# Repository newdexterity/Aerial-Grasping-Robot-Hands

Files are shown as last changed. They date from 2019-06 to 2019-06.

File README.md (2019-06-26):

# Aerial-Grasping-Robot-Hands
## Introduction
Over the last decade, a new class of adaptive robot hands has been proposed that facilitates the execution of stable grasps in unstructured environments even when the object properties are not known. This attribute of adaptive hands is due to the under-actuation and their mechanical compliance that allow them to conform to the object surface. 

This adaptive robot hand is designed for UAV-based autonomous package delivery problem. Therefore, the robot hand must be extremely quick (< 100 ms), [lightweight](https://github.com/newdexterity/Aerial-Grasping-Robot-Hands/blob/master/Media/weight_analysis_aerial_gripper.pdf) (< 505 g), provide reliable grasping and enable perching for aerial platforms such as UAVs.

## Prototype
The prototype of this aerial grasping robot hand is designed by [New Dexterity Research Team](https://www.newdexterity.org/) from the University of Auckland.

<p align="center">
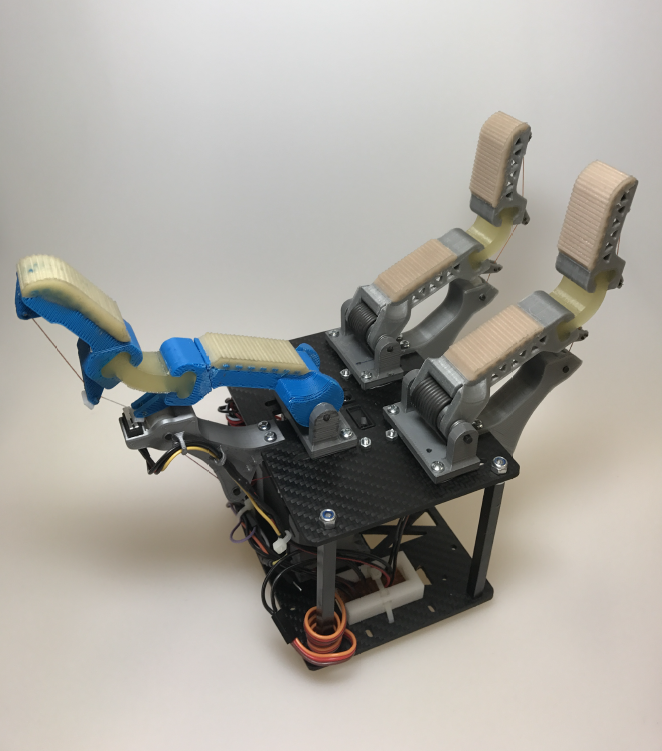
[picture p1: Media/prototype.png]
  
</p>

<p align="center"> 
  Figure 1. Prototype of the aerial grasping robot hand
</p>

## Quick release mechanism
A novel quick release mechanism which contains two servomotors has been proposed in this paper. The quick release mechanism allows the main servomotor to winch the tendons and open each finger. When the other servomotor is actuated, the dog collar disengages with the 35T spur gear, allowing the dog collar and the drum to rotate freely.

<p align="center">
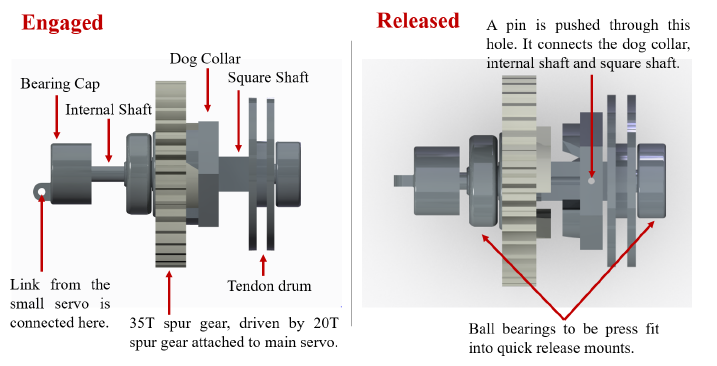
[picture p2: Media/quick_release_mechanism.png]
  
</p>

<p align="center"> 
  Figure 2. Quick release mechanism
</p>                                           

## Sensors
* [Infrared sensor](http://www.sharp-world.com/products/device/lineup/data/pdf/datasheet/gp2y0a21yk_e.pdf)

## Contents
In this repository you can find:
* CAD files of an ultra-fast aerial grasping robot hand
* Archive of prototype images
* Arduino code for controling this robot hand

## Notes
Please open a [Github issue](https://github.com/newdexterity/Aerial-Grasping-Robot-Hands/issues) if you encounter any problem.

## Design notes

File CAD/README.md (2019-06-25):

## Robot Hands CAD files
In this folder we provide appropriate 3D models (Solidworks .SLDPRT) and files for 3d printer (.stl) in order to replicate the proposed design. This aerial grasping robot hand has an improved mechanical structure design and a shell to protect the quick release mechanism compared with the prototype.

<p align="center">
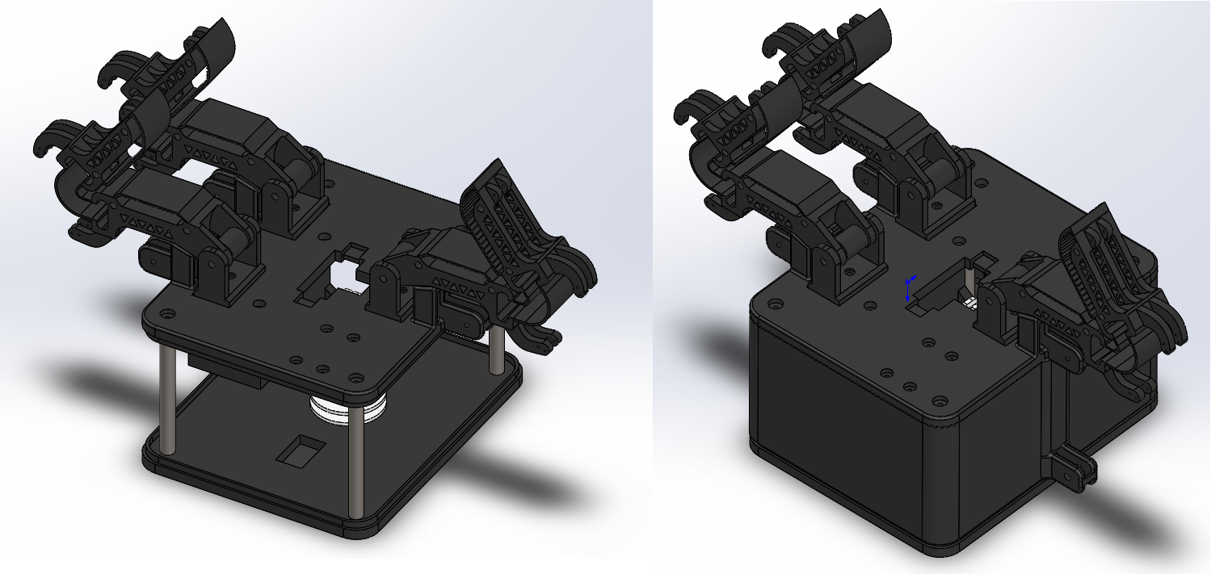
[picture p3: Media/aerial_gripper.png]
  
</p>

<p align="center"> 
  Figure 3. The appearance of the aerial grasping robot hand.
</p>    
                                           
## Modeling
If you need some help on modeling fingers, please take a look at the instruction [here](https://www.eng.yale.edu/grablab/openhand/OpenHand%20Finger%20Guide.pdf).

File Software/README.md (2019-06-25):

## Introduction
In order to control the robot hand, we use one OpenCM9.04-C board and two Dynamixel motors (XM430-350-T). Please click [here](http://www.robotis.us/dynamixel/) for more information about Dynamixel motors.
## OpenCM9.04
OpenCM9.04 is a microcontroller board based on 32bit ARM Cortex-M3. The OpenCM9.04’s schematics and source codes are open-source. Please click [here](http://emanual.robotis.com/docs/en/parts/controller/opencm904/) for more information about OpenCM9.04.

The connections between OpenCM9.04-C board and other devices are shown in Fig. 4:
<p align="center">
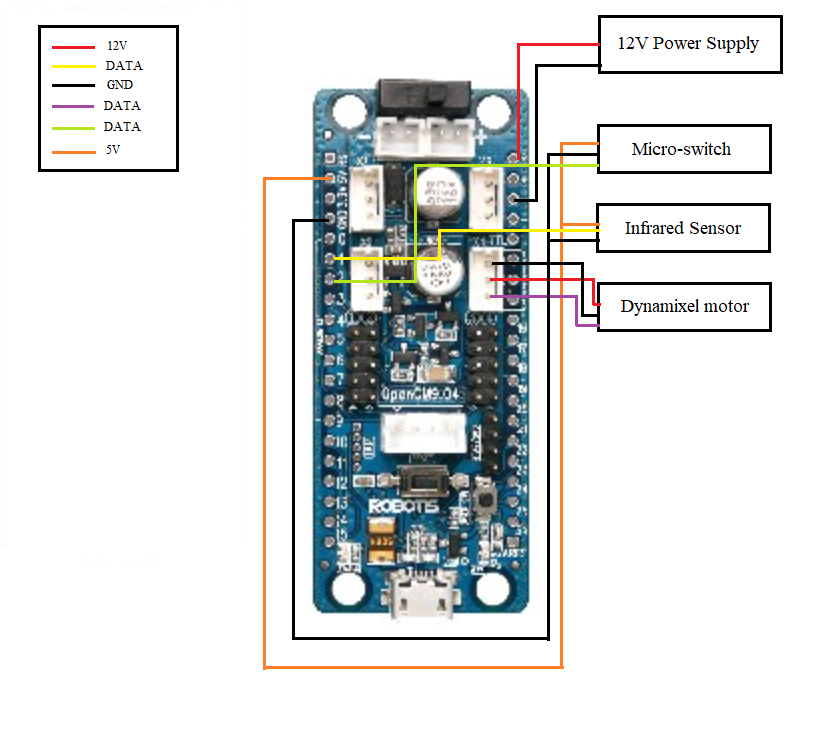
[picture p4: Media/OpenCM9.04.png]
  
</p>

<p align="center"> 
  Figure 4. Connections between OpenCM9.04-C and other devices.
</p>   
                                        
## IDE
As OpenCM IDE will not be updated anymore, we recommend users to code on Arduino IDE for OpenCM9.04-C board. Here is the instruction for installing OpenCM9.04 package on Arduino IDE:

<p align="center">
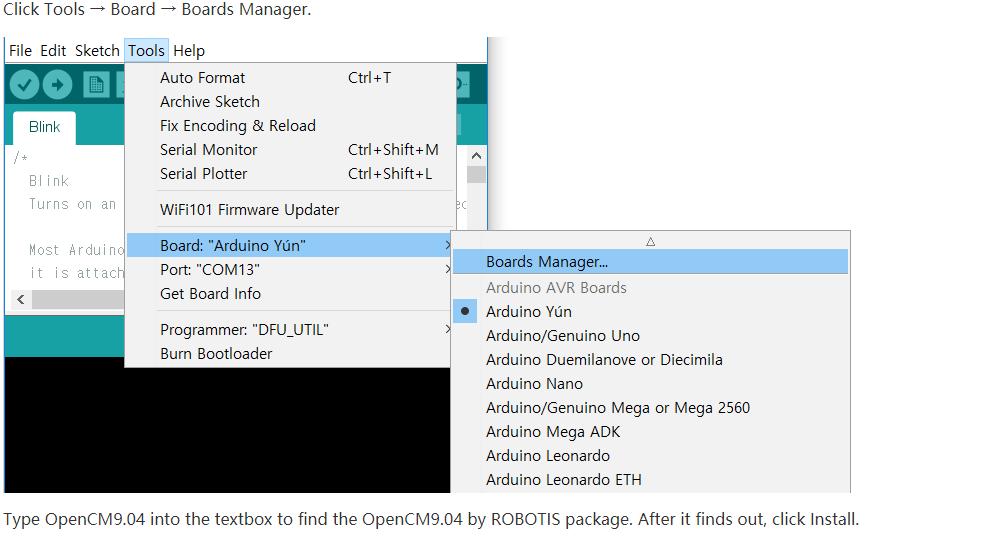
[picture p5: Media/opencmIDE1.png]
  
</p>

<p align="center">
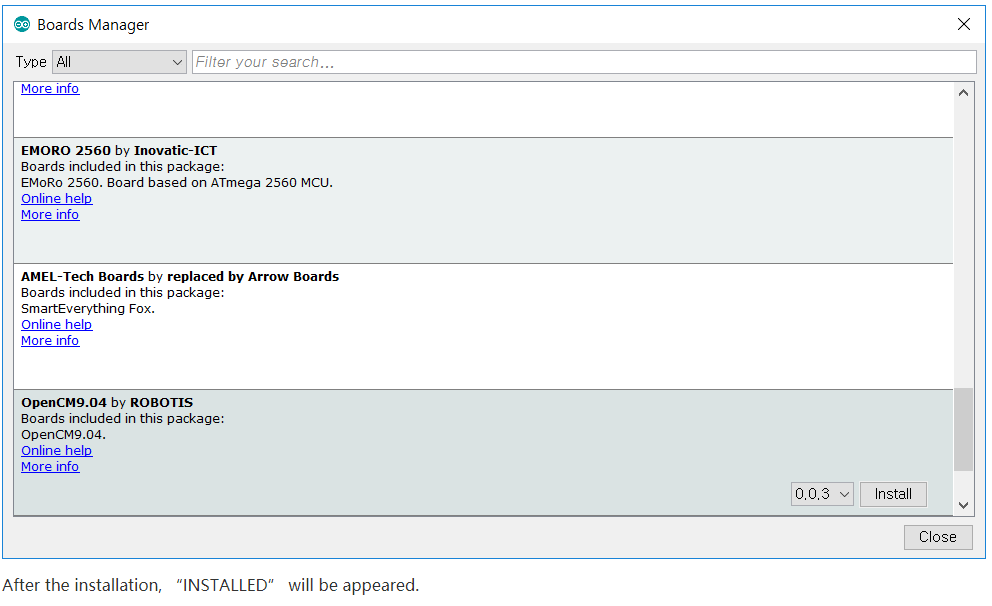
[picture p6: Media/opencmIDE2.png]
  
</p>

<p align="center">
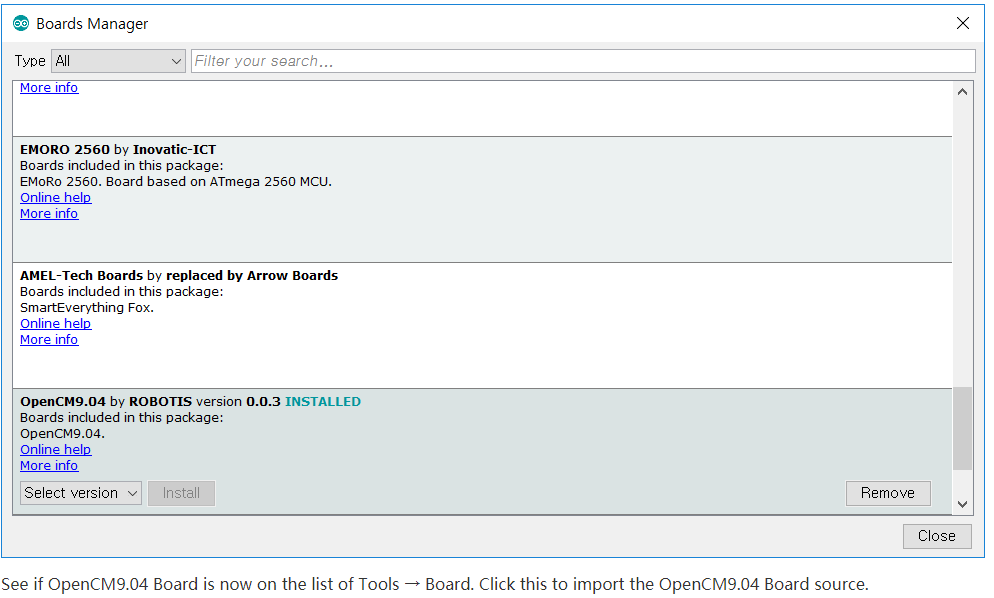
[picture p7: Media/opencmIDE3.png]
  
</p>

<p align="center">
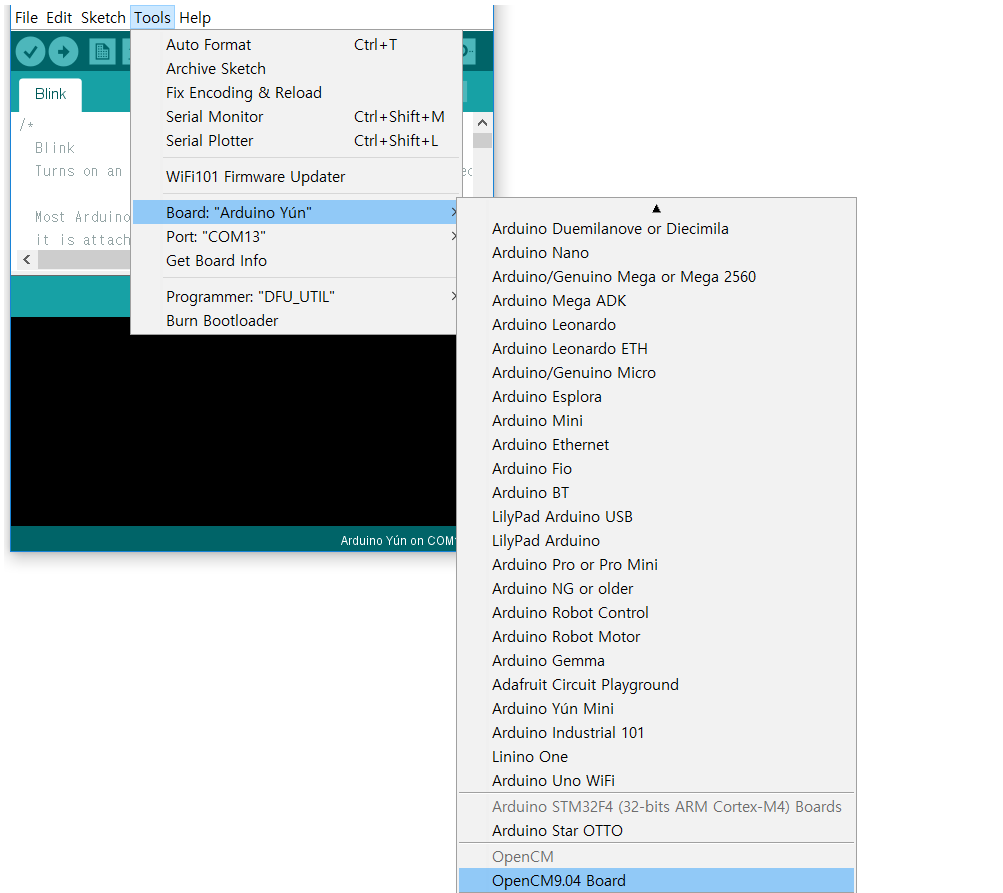
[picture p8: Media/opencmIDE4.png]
  
</p>

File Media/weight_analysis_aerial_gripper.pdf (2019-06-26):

Table I. Weight Analysis for Aerial Grasping Robot Hand

Part# | Name | Quantity | Total Weight (g)
Finger Components
1 | Finger | 3 | 90
2 | Finger Base | 3 | 9
3 | Finger Part | 3 | 3
Robot Hand Base Components
4 | Upper Plate | 1 | 64
5 | Shell | 1 | 36
6 | Lower Plate | 1 | 38
Other Components on Robot Hand Base
7 | OpenCM Support | 4 | < 4
8 | Dynamixel Motor Support | 1 | 17
9 | Base Support | 4 | 7
10 | Rotating Wheel | 6 | < 2
Quick Release Mechanism
11 | Rotating Wheel 1 | 1 | < 2
12 | Rotating Wheel 2 | 1 | < 4
13 | Bearing Cap | 1 | < 1
14 | Dog Collar | 1 | < 1
15 | Spur Gear | 1 | < 5
16 | Square Shaft | 1 | < 1
17 | Tendon Drum | 1 | < 3
Other Components
18 | Dynamixel XM430-350-T | 2 | 164
19 | OpenCM9.04-C | 1 | 13
20 | Bearing | 3 | 9
21 | Screws | 42 | <13
22 | Nuts | 4 | < 2

23 | Infrared Sensor | 1 | 5
24 | Mirco-switcher | 1 | < 3
25 | Springs | 3 | 9
Total Weight
| | | < 505

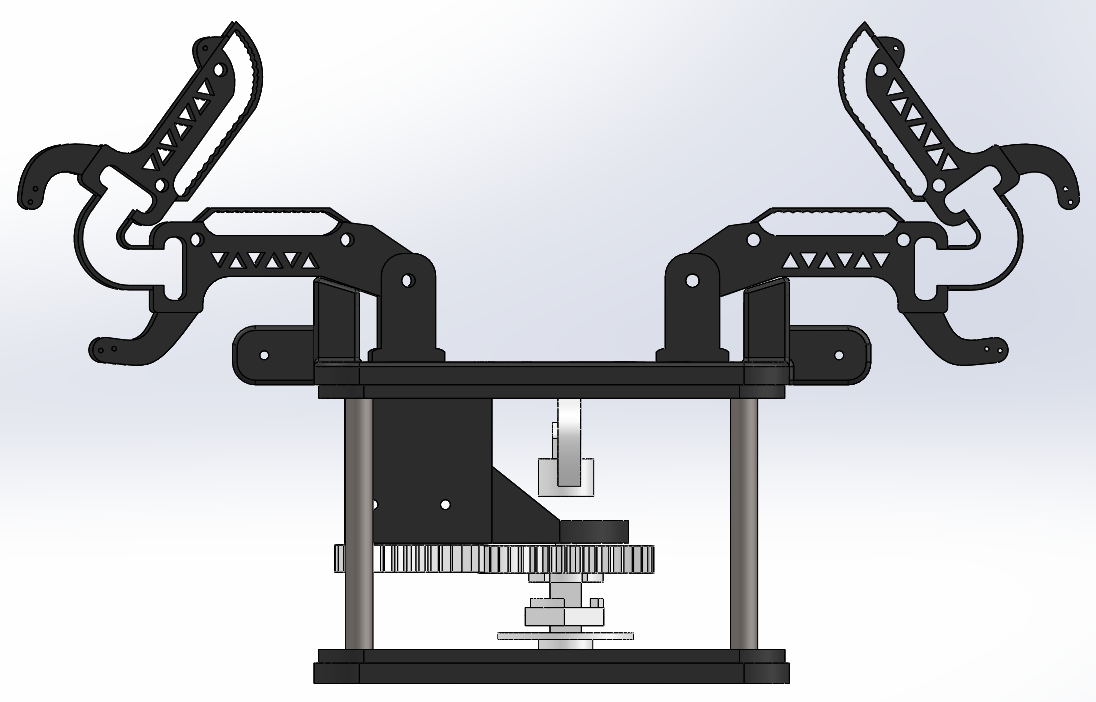
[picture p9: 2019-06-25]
Media/frontView.png

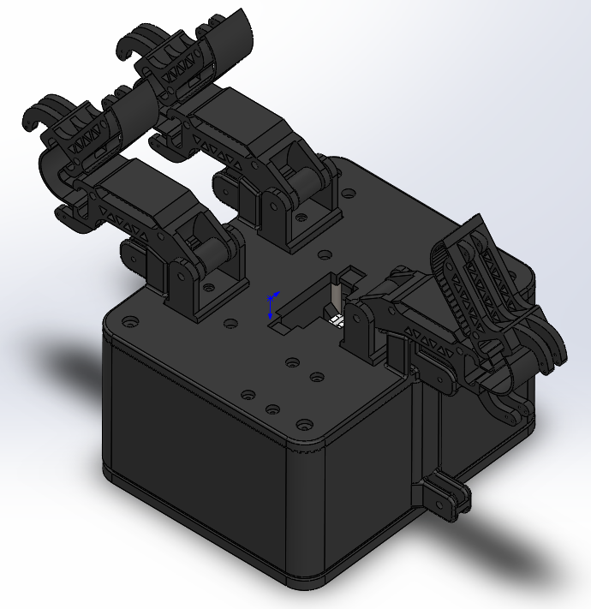
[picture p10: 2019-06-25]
Media/aerial_gripper_with_shell.png

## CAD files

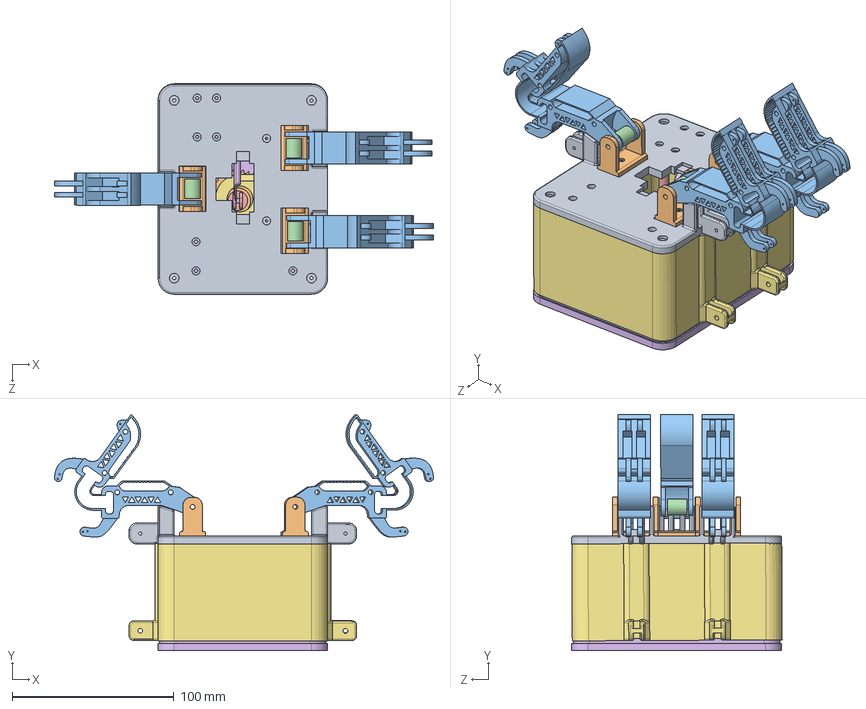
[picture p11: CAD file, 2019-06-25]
CAD/aerial_grasping_robot_hand.SLDASM
234.6 x 146.2 x 130.3 mm
baseLowerPlate
fingerBase x 3
finger x 3
fingerPart x 3
baseSupport x 4
baseUpperPlate
ServoSupport
rotatingWheel1
squareShaft
spurGear
dogCollar
tendonDrum
bearingCap
rotatingWheel2
baseShell

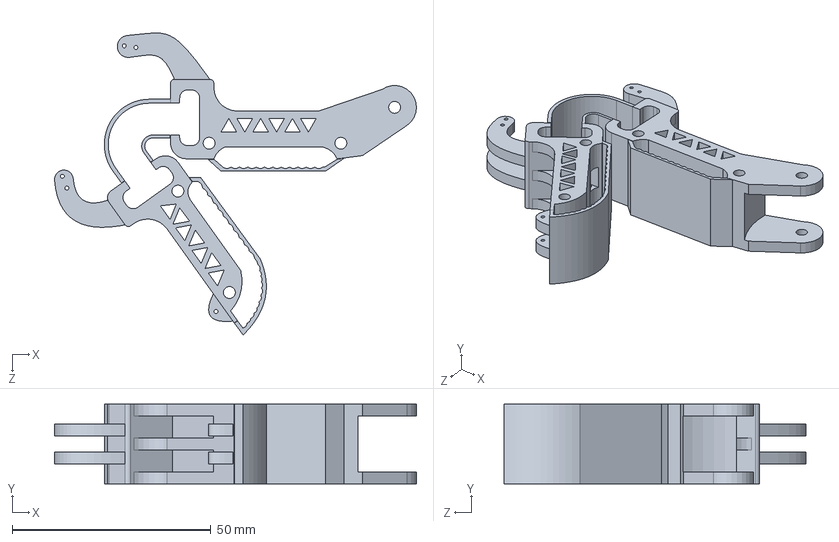
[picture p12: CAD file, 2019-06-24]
CAD/Finger/finger.SLDPRT
91.0 x 20.0 x 75.9 mm

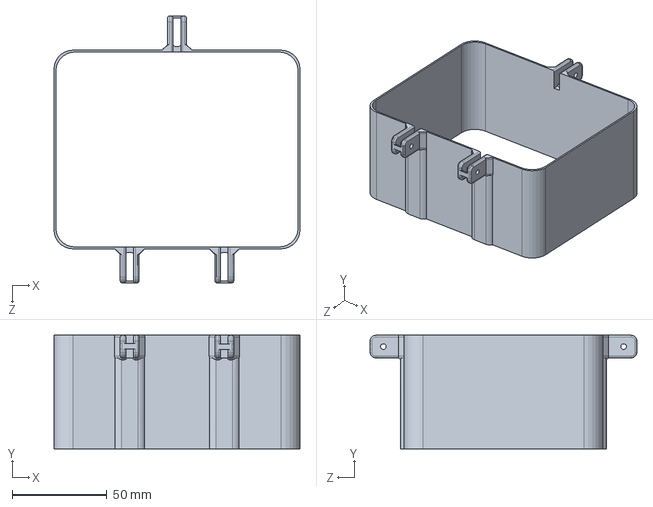
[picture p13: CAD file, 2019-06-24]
CAD/RobotHandBase/baseShell.SLDPRT
130.0 x 60.0 x 141.0 mm

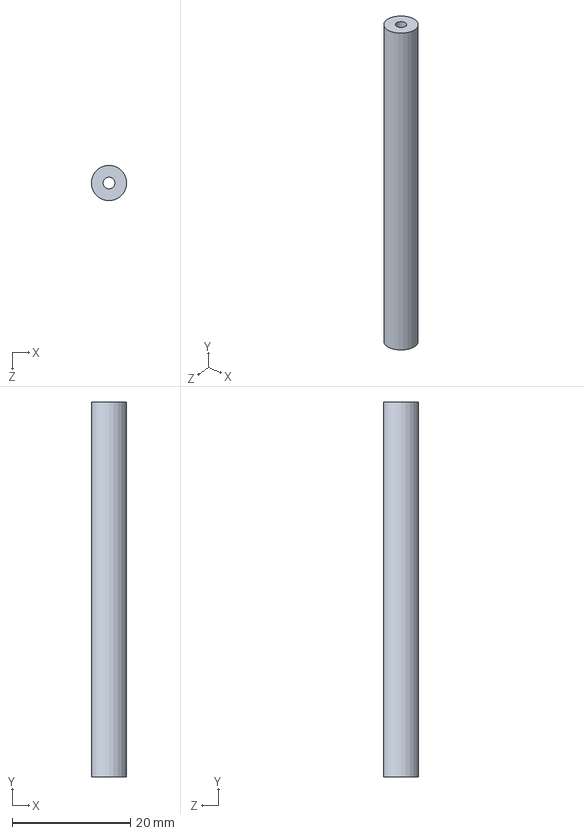
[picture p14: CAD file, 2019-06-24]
CAD/RobotHandBase/commonParts/baseSupport.SLDPRT
6.00 x 63.5 x 6.00 mm

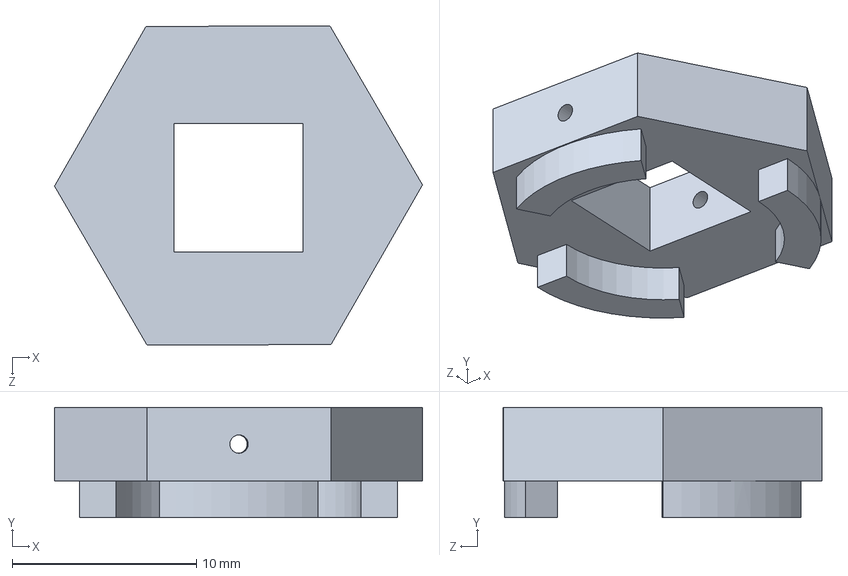
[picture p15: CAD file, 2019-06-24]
CAD/RobotHandBase/quickReleaseMechanism/dogCollar.SLDPRT
20.0 x 6.00 x 17.4 mm

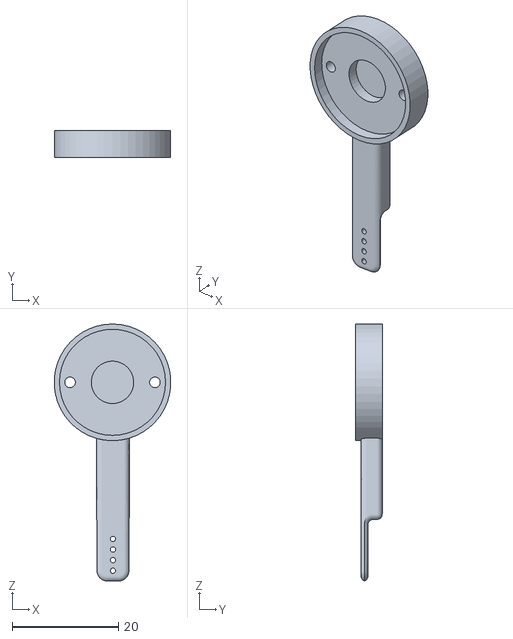
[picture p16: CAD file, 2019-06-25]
CAD/STL/rotatingWheel2.STL
21.9 x 5.00 x 48.5

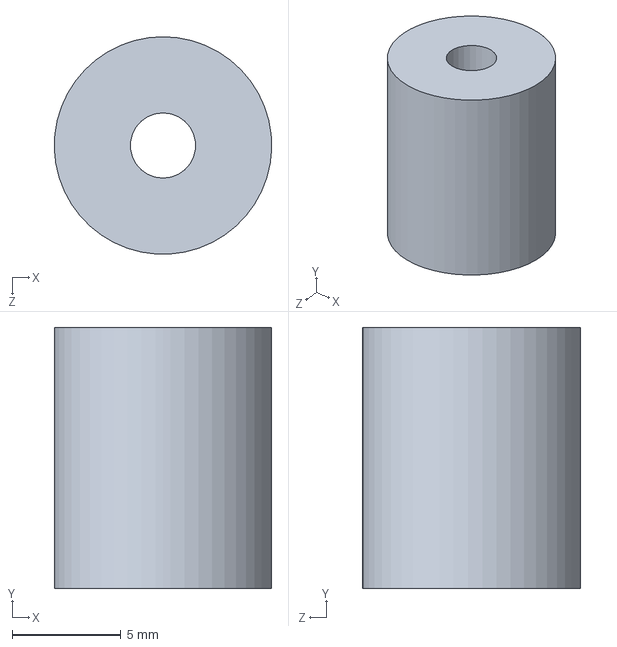
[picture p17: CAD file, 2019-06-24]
CAD/Finger/fingerPart.SLDPRT
9.99 x 12.0 x 10.0 mm

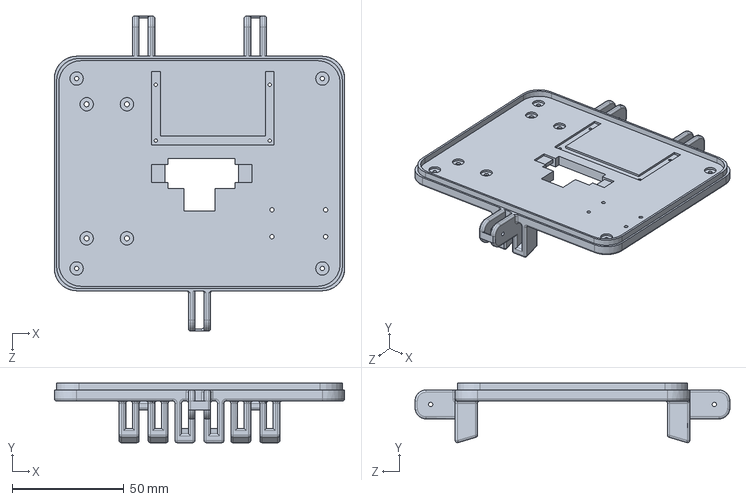
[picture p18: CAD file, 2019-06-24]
CAD/RobotHandBase/baseLowerPlate.SLDPRT
130.0 x 26.7 x 141.0 mm

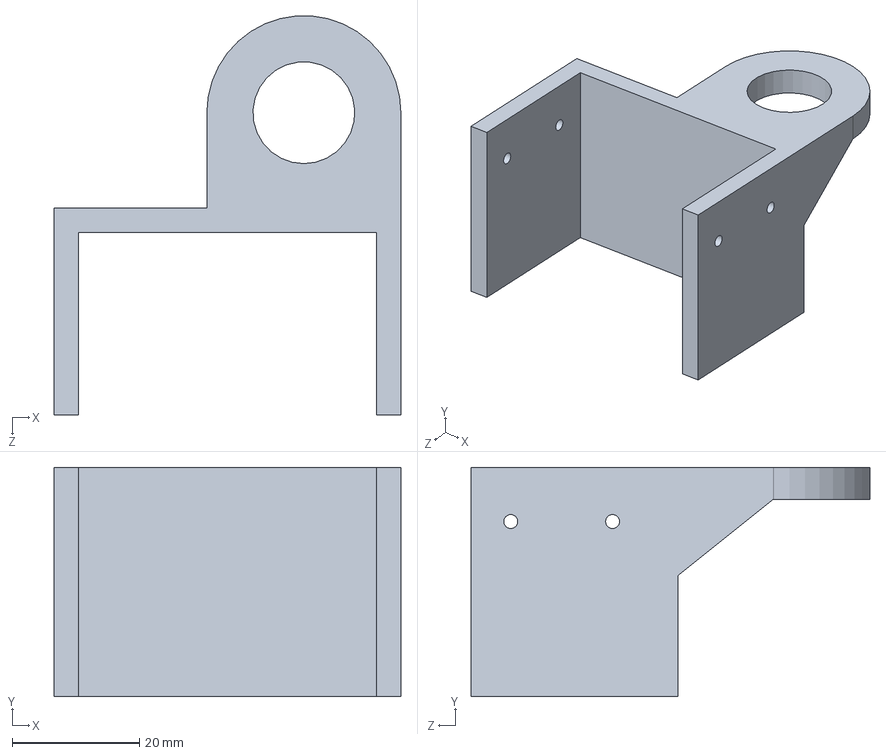
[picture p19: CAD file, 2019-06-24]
CAD/RobotHandBase/commonParts/ServoSupport.SLDPRT
54.5 x 36.0 x 62.7 mm

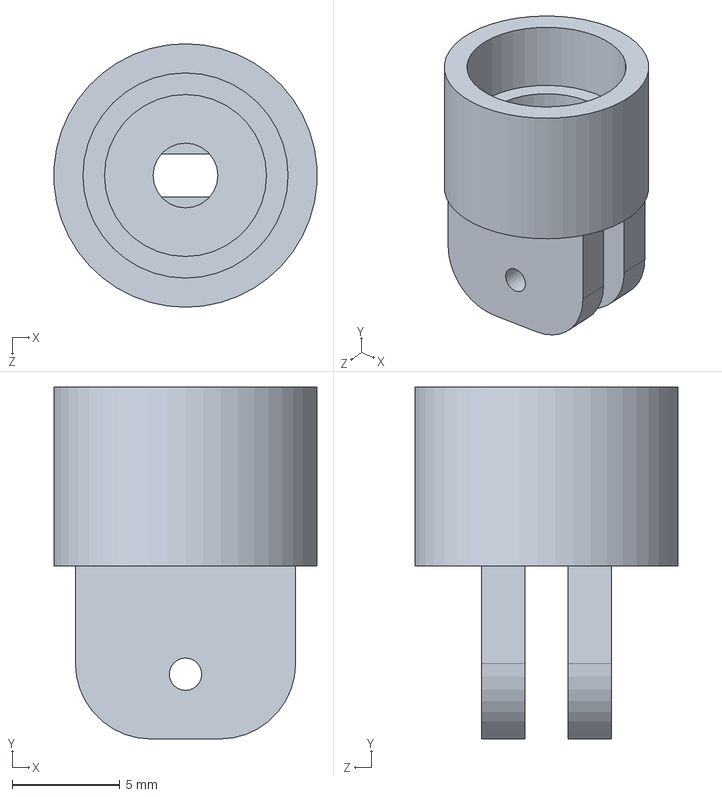
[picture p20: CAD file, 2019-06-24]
CAD/RobotHandBase/quickReleaseMechanism/bearingCap.SLDPRT
12.2 x 16.3 x 12.2 mm

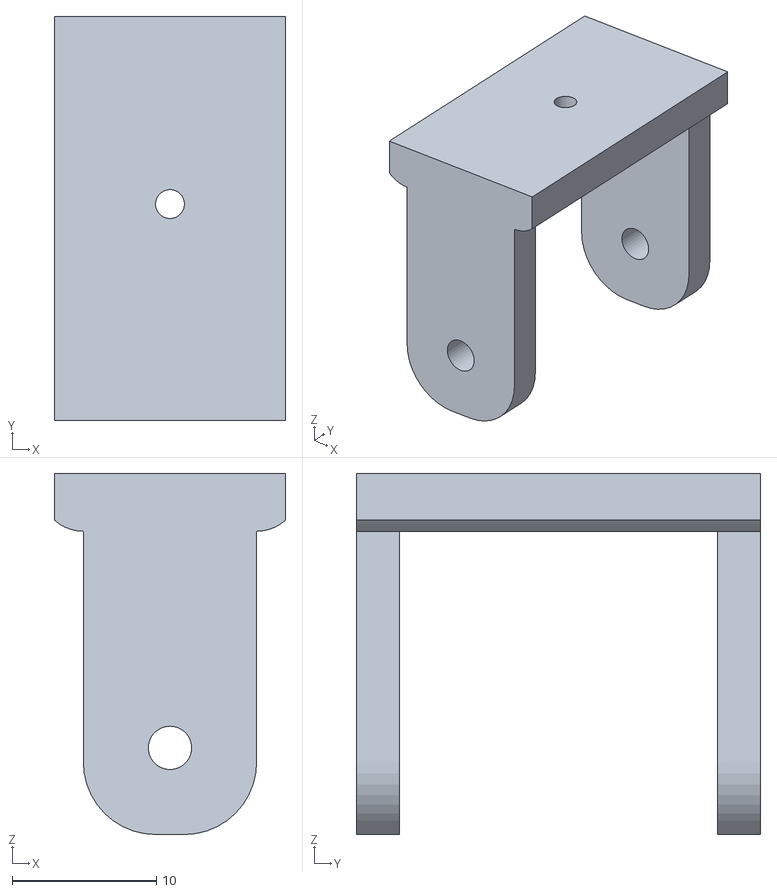
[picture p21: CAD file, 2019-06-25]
CAD/STL/fingerBase.STL
16.0 x 28.0 x 25.0

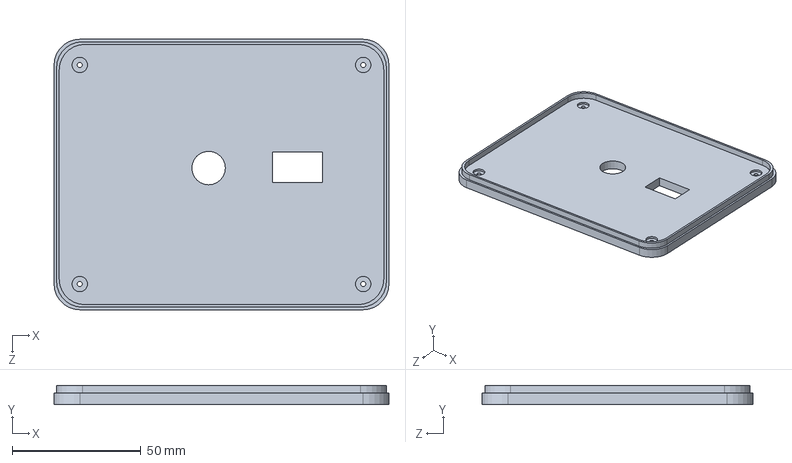
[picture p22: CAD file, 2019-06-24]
CAD/RobotHandBase/baseUpperPlate.SLDPRT
130.0 x 7.50 x 105.0 mm

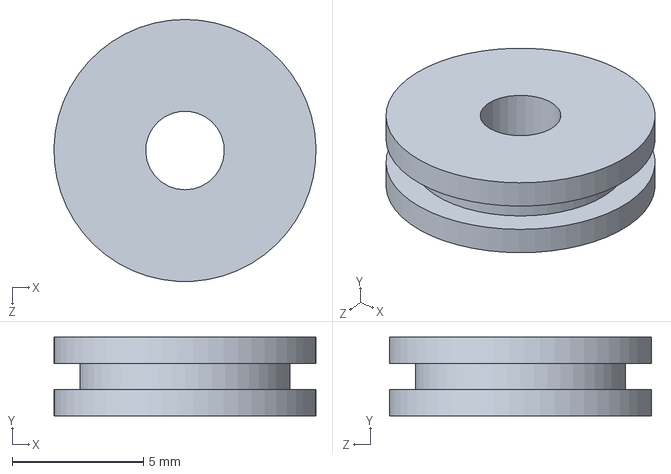
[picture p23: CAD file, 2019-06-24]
CAD/RobotHandBase/commonParts/rotatingWheel.SLDPRT
10.00 x 3.00 x 10.0 mm

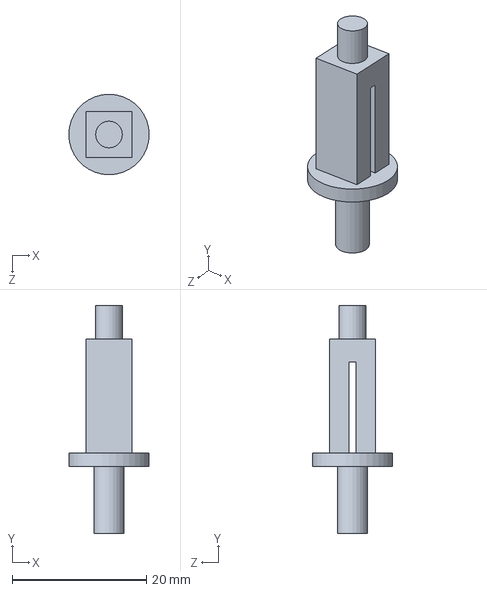
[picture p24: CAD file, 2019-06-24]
CAD/RobotHandBase/quickReleaseMechanism/squareShaft.SLDPRT
12.0 x 34.0 x 12.0 mm

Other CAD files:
CAD/Finger/fingerBase.SLDPRT
CAD/STL/rotatingWheel.STL
CAD/RobotHandBase/commonParts/OpencmSupport.SLDPRT
CAD/RobotHandBase/quickReleaseMechanism/tendonDrum.SLDPRT
CAD/RobotHandBase/quickReleaseMechanism/rotatingWheel1.SLDPRT
CAD/RobotHandBase/quickReleaseMechanism/rotatingWheel2.SLDPRT
CAD/RobotHandBase/quickReleaseMechanism/spurGear.SLDPRT
CAD/STL/OpencmSupport.STL
CAD/STL/ServoSupport.STL
CAD/STL/baseLowerPlate.STL
CAD/STL/baseShell.STL
CAD/STL/baseSupport.STL
CAD/STL/baseUpperPlate.STL
CAD/STL/bearingCap.STL
CAD/STL/dogCollar.STL
CAD/STL/finger.STL
CAD/STL/fingerPart.STL
CAD/STL/rotatingWheel1.STL
CAD/STL/spurGear.STL
CAD/STL/squareShaft.STL
CAD/STL/tendonDrum.STL

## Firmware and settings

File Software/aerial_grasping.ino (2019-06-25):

/************************** Aerial Gripper Code ***********************/
/************************** Author: Jiawei Meng ***********************/
/*************************** Date: 14/06/2019 *************************/
/*** Description: This code is the first version for aerial gripper ***/

#include <DynamixelWorkbench.h>  

/******************** Definitions of parameters ***********************/

#if defined(__OPENCM904__)
  #define DEVICE_NAME "1"               //Dynamixel on Serial3(USART3)  <-OpenCM 485EXP or Dynamixel on Serial1(USART1)  <-OpenCM 9.04
#elif defined(__OPENCR__)
  #define DEVICE_NAME ""
#endif 

#define BAUDRATE  57600

#define IR_PIN 1                        //Define the pin of the IR sensor
#define SWITCHER_PIN 2                  //Define the pin of the switcher

#define TRIGGER 0                       //Define the state of the switcher
#define HOVER 1

DynamixelWorkbench dxl_wb;

int val_ir = 0;
int switcher = 0;

uint8_t dxl_id1 = 2;
uint8_t dxl_id2 = 1;

uint16_t model_number1 = 0;
uint16_t model_number2 = 0;


/************************* Set intial status **************************/
void setup() 
{ 
  Serial.begin(BAUDRATE);                                  //Set the Baud rate of the serial port
  
  while(!Serial);                                          // Wait for Opening Serial Monitor

  const char *log;                                         // The code start to initialise motor 1 and motor 2
  bool result = false;

  result = dxl_wb.init(DEVICE_NAME, BAUDRATE, &log);        //Intialise the OpenCM9.04 board
  if (result == false)
  {
    Serial.println(log);
    Serial.println("Failed to init the OpenCM9.04");
  }
  else
  {
    Serial.print("Succeeded to init OpenCM9.04: ");
    Serial.println(BAUDRATE);  
  }

  result = dxl_wb.ping(dxl_id1, &model_number1, &log);       //Ping the 1st DYNAMIXEL motor        
  if (result == false)
  {
    Serial.println(log);
    Serial.println("Failed to ping motor 1");
  }
  else
  {
    Serial.println("Succeeded to ping motor 1");
    Serial.print("id : ");
    Serial.print(dxl_id1);
    Serial.print(" model_number : ");
    Serial.println(model_number1);
  }

  result = dxl_wb.ping(dxl_id2, &model_number2, &log);        //Ping the 2nd DYNAMIXEL motor          
  if (result == false)
  {
    Serial.println(log);
    Serial.println("Failed to ping motor 2");
  }
  else
  {
    Serial.println("Succeeded to ping motor 2");
    Serial.print("id : ");
    Serial.print(dxl_id2);
    Serial.print(" model_number : ");
    Serial.println(model_number2);
  }

  result = dxl_wb.currentBasedPositionMode(dxl_id1, 200, &log);  //Set current-based position control for motor 1 with 30 mA current limitation
  if (result == false)
  {
    Serial.println(log);
    Serial.println("Failed to change current based position mode for motor 1");
  }
  else
  {
    Serial.println("Succeed to change current based position mode for motor 1");
  }

  result = dxl_wb.currentBasedPositionMode(dxl_id2, 200, &log);  //Set current-based position control for motor 2 with 30 mA current limitation
  if (result == false)
  {
    Serial.println(log);
    Serial.println("Failed to change current based position mode for motor 2");
  }
  else
  {
    Serial.println("Succeed to change current based position mode for motor 2");
  }

  dxl_wb.goalPosition(dxl_id1, (int32_t)0);           //Set the initial positions of motor 1

  dxl_wb.goalPosition(dxl_id2, (int32_t)920);         //Set the initial positions of motor 2
  
  pinMode(IR_PIN, INPUT_ANALOG);                      //Set port 1 to read the analog value of IR sensor

  pinMode(SWITCHER_PIN, INPUT_PULLDOWN);              //Set port 2 to read the value of the switcher ('0' is pushing state and '1' is idle state)

}


/************************* Main loop function *************************/
void loop() 
{ 
  val_ir = readIR();
  
  switcher = digitalRead(SWITCHER_PIN);

  Serial.print("switcher is ");
  
  Serial.println(switcher);

  // If the switcher is not closed, then the palm starts to open
  if(switcher == HOVER)
  {
    int lock_interval_1 = 0;
    int load_interval = 0;
  
    dxl_wb.goalPosition(dxl_id1, (int32_t)0);
    
    delay(1000);

//    dxl_wb.goalPosition(dxl_id2, (int32_t)820);
    
    for(int count = 0; count < 8; count++)                        //Locking the quick release device
    {
        dxl_wb.goalPosition(dxl_id1, (int32_t)lock_interval_1);
        delay(500);
        dxl_wb.goalPosition(dxl_id2, (int32_t)820);
        delay(500);
        lock_interval_1 = lock_interval_1 + 40;
    }
    
    delay(1000);

    while(switcher == HOVER)
    {
      load_interval = load_interval + 10;
      
      dxl_wb.goalPosition(dxl_id1, (int32_t)load_interval);
      
      switcher = digitalRead(SWITCHER_PIN);
    }
    
    // If the switcher is closed and an object is sensed within range, then the palm starts to close
    while(val_ir < 600)
    {
      val_ir = readIR();
    }
    dxl_wb.goalPosition(dxl_id2, (int32_t)920);
  
    delay(10000);
  }
}



/**************************** Read IR sensor **************************/
int readIR()
{
  int sensor_val = 0;
  
  for(int i = 0; i < 10; i++)
  {
    sensor_val = sensor_val + analogRead(IR_PIN);              //Read the value of IR sensor from 'IR_PIN'
  }
  
  sensor_val = sensor_val/10.0;
  
  Serial.print("IR sensor is ");
  
  Serial.println(sensor_val);

  return sensor_val;                                //Return the value for this function
}
